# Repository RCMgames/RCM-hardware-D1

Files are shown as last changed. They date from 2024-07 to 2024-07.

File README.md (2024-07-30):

# RCM-hardware-D1

v1.0

* 1.75 by 1.575 inches, 44.45 by 40.0 millimeters
* 2 motors (one L293D)
* 2 servos OR qwiic connector
* Qwiic-Compatible
* runs on 4 NiMH AAs
* battery monitoring
* uses a Wemos D1 mini with esp8266 CPU

The goal of this project is to make the cheapest [RCM board](https://github.com/rcmgames).

Program with [RCMv2](https://github.com/rcmgames/rcmv2)

The RCM D1 uses a Wemos D1 mini v4.0.0 esp8266 board. 

Use the AVR versions of JMotor functions not the ESP32 versions.

## Options for purchasing

* [PCBWay link](https://www.pcbway.com/project/shareproject/Cheap_wifi_connected_Robot_Control_Module_RCM_D1_v1_0_a19b71a2.html)
* send the gerbers to a PCB manufacturer of your choice

## Components
Solder by hand to assemble your boards.
| part | links | quantity | notes |
| ----- | ----- | ----- | ----- |
| RCM D1 circuit board | see options for purchasing above | 1 | |
| Wemos D1 mini with esp8266 | [link](https://www.wemos.cc/en/latest/d1/d1_mini.html) | 1 | |
| L293D | [digikey](https://www.digikey.com/en/products/detail/texas-instruments/L293DNE/379724) | 1 | |
| 16 pin IC socket | | 1 | optional |
| 18k resistor | [digikey](https://www.digikey.com/en/products/detail/stackpole-electronics-inc/RNMF14FTC18K0/2617300) | 1 | R1 |
| 10k resistor | [digikey](https://www.digikey.com/en/products/detail/yageo/MFR-12FTF52-10K/9133815) | 1 | R2 |
| 47uF capacitor | [digikey](https://www.digikey.com/en/products/detail/rubycon/63ZLJ47M6-3X11/3134467) | 1 | |
| Qwiic connector (JST SH) | [digikey](https://www.digikey.com/en/products/detail/jst-sales-america-inc/SM04B-SRSS-TB/926710) | 1 | optional, for qwiic connector |
| 2x3 male header pins | | 1 | for servos |
| 2 female header pins | | 2 | for motors |
| 8 female header pins | | 2 | often included with the wemos D1 |
| 8 male header pins | | 2 | often included with the wemos D1 |
| battery wires | [JST RCY](https://www.amazon.com/dp/B00Z04QFN2/) or battery plug of your choice | 1 | |

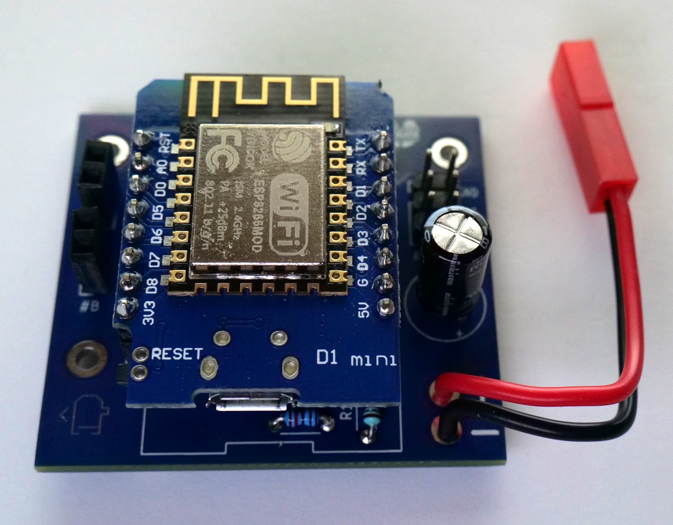
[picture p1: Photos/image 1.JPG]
photo of assembled board


## Acknowledgements

The RCM D1 was originally created for [PNW Assistive Technology's RC car project](https://github.com/PNW-AT/rc-car-car)

Thanks for the WemosD1 Kicad footprints! https://github.com/rubienr/wemos-d1-mini-kicad

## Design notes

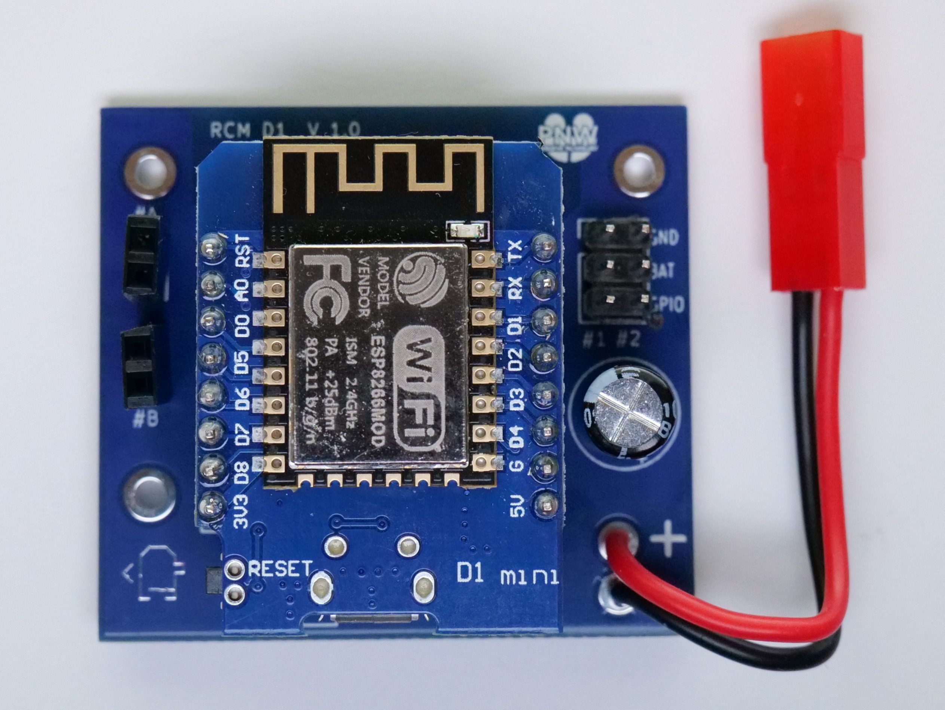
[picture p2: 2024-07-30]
Photos/top.JPG

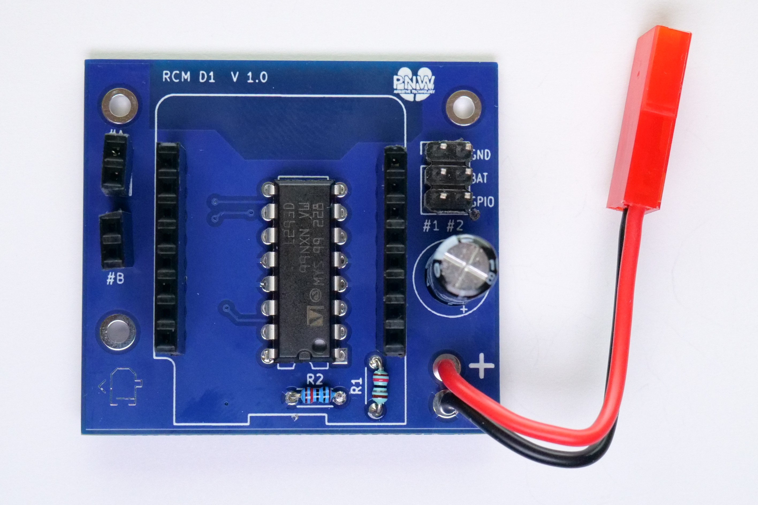
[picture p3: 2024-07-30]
Photos/without esp.JPG

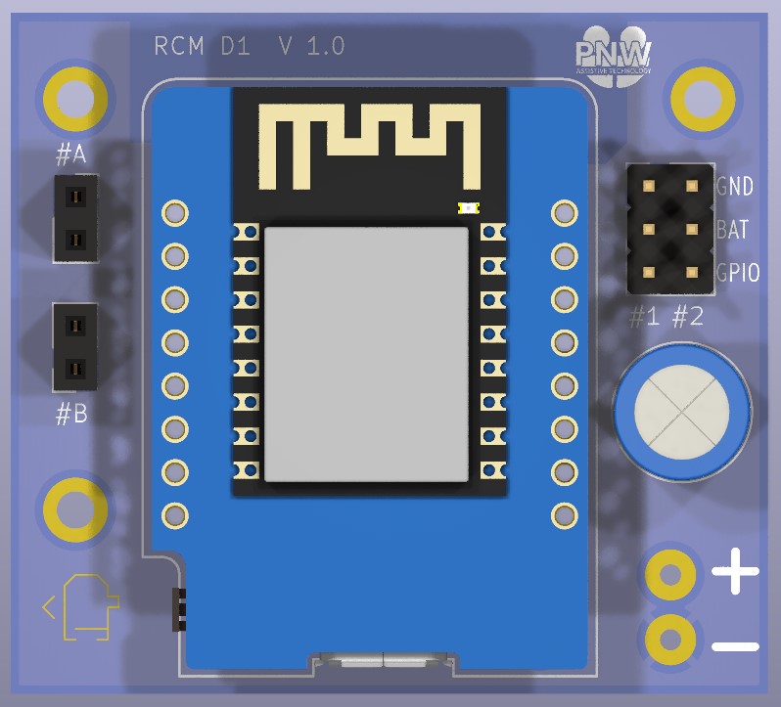
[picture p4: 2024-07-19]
CAD renders/front.jpg

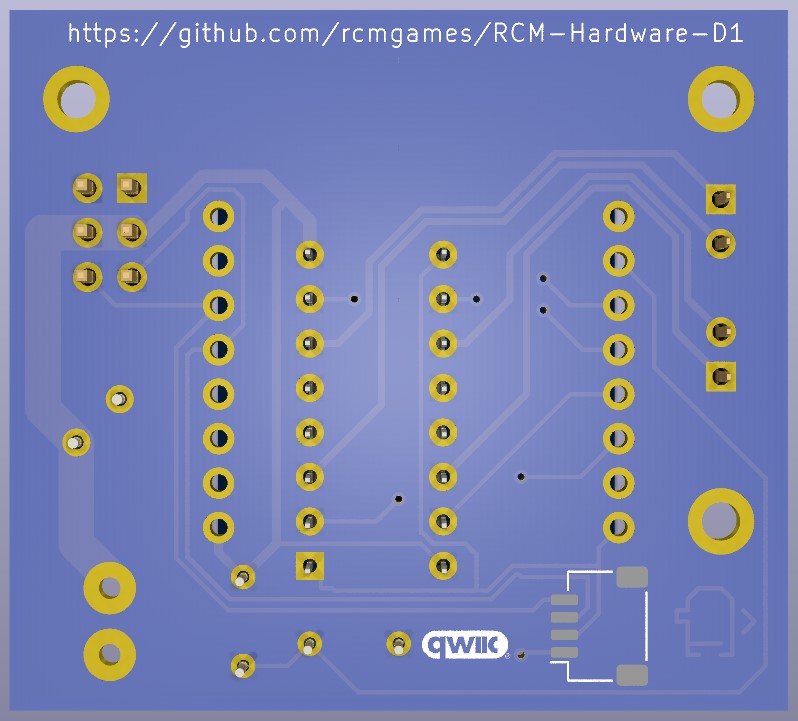
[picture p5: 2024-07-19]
CAD renders/back.jpg

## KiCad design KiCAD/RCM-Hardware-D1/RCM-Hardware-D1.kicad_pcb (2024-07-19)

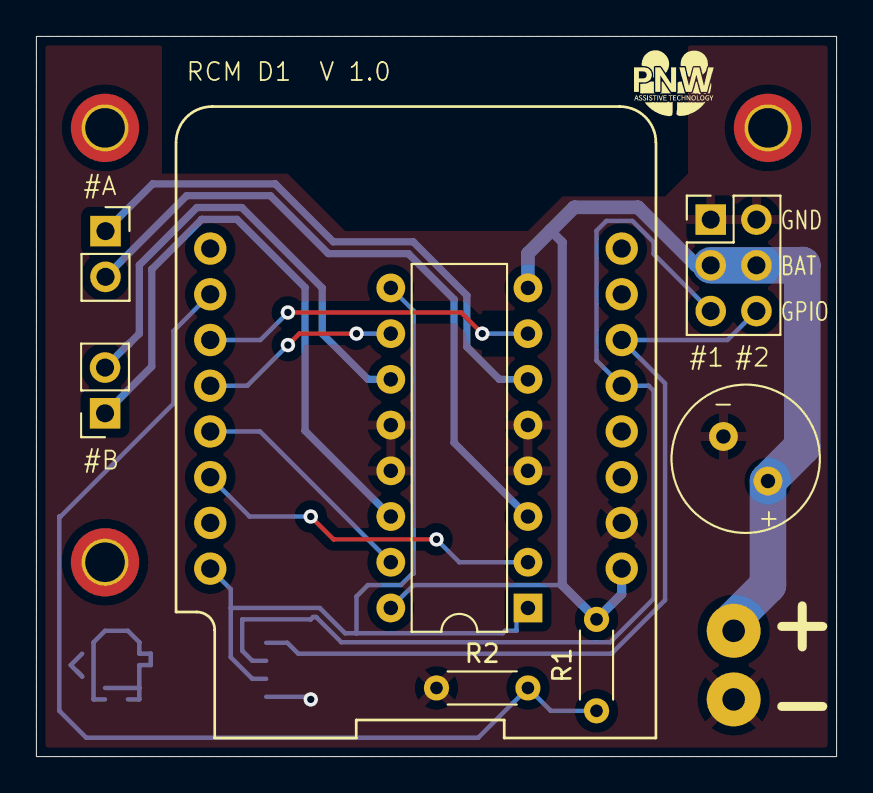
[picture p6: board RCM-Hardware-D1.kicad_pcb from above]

Board: 2 copper layers, 44.4 x 40.0 mm, 10 parts (1 on the bottom side), 14 nets.

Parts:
C1: C_Polarized; C_Radial_D8.0mm_H11.5mm_P3.50mm
J1, J2: Conn_01x02_Pin; PinSocket_1x02_P2.54mm_Vertical
J3: battery; battery wires
J6: Conn_01x04_Pin; JST_SH_SM04B-SRSS-TB_1x04-1MP_P1.00mm_Horizontal
J7: Conn_01x06_Pin; PinHeader_2x03_P2.54mm_Vertical
R1, R2: R; R_Axial_DIN0204_L3.6mm_D1.6mm_P5.08mm_Horizontal
U1: WeMos_D1_mini; wemos-d1-mini-with-pin-header
U2: L293D; DIP-16_W7.62mm

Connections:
+3.3V: J6.2, U1.8 (3.3V), U2.1 (EN1,2), U2.9 (EN3,4)
GND: C1.2, J3.2, J6.1, J7.1, J7.2, R2.1, U1.10 (GND), U2.4 (GND), U2.5 (GND), U2.12 (GND), U2.13 (GND)
unnamed: J1.1, U2.14 (4Y)
unnamed: J1.2, U2.11 (3Y)
unnamed: J2.1, U2.6 (2Y)
unnamed: J2.2, U2.3 (1Y)
unnamed: C1.1, J3.1, J7.3, J7.4, R1.2, U1.9 (5V), U2.8 (VCC2), U2.16 (VCC1)
unnamed: J6.3, J7.5, U1.13 (D2)
unnamed: J6.4, J7.6, U1.14 (D1)
unnamed: R1.1, R2.2, U1.2 (A0)
unnamed: U1.3 (D0), U2.7 (2A)
unnamed: U1.4 (D5), U2.10 (3A)
unnamed: U1.5 (D6), U2.15 (4A)
unnamed: U1.6 (D7), U2.2 (1A)

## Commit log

2024-06-03 initial KiCAD commit
    [RCM-Hardware-D1.kicad_pcb, RCM-Hardware-D1.kicad_sch]
2024-06-04 set up kicad
    [RCM-Hardware-D1.kicad_pcb, RCM-Hardware-D1.kicad_sch]
2024-06-04 update kicad
    [RCM-Hardware-D1.kicad_pcb, RCM-Hardware-D1.kicad_sch]
2024-07-19 Continued the KeyCAD for the circuit board
    [RCM-Hardware-D1.kicad_pcb, RCM-Hardware-D1.kicad_sch]
2024-07-19 finished the KiCAD and created Gerbers
    [RCM-Hardware-D1.kicad_pcb, RCM-Hardware-D1.kicad_sch]
